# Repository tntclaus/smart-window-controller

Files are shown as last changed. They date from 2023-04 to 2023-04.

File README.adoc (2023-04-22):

# Контроллер умного окна

[.float-group]
--
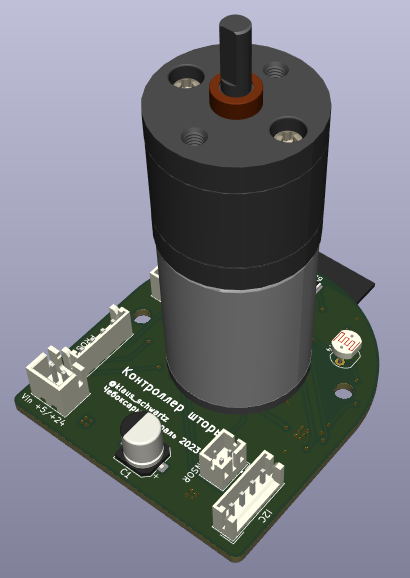
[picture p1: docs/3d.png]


Устройство для управления рулонной шторой. Умеет:

1. Прятаться внутри трубы рулонной шторы. Ставится с другого конца от механической крутилки и имеет такой же габарит. Механическая крутилка сохраняется т.к. вручную шторами тоже удобно управлять.
2. Двигать шторой, в том числе зеброй.
3. Датчиком освещенности следить, чтобы шторы пропускали необходимое количество света.может делиться этой инфой с другими шторами.
4. Датчиком холла контролить текущее положение шторы, даже если шторой управляют вручную через цепочку.
5. Автокалибровать положения полностью свернутой шторы концевиком если пропало электричество и штору двигали вручную.
6. Общаться с дополнительной переферией по i2c / uart (если есть).
7. Опрашивать датчик открытого окна (если есть).
--

## Печатные платы

Дизайн в kicad. Печатная плата распаивается непосредственно на двигатель.

[.float-group]
--
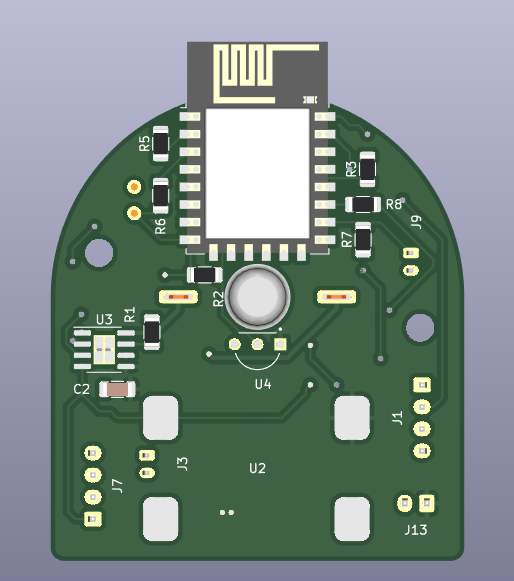
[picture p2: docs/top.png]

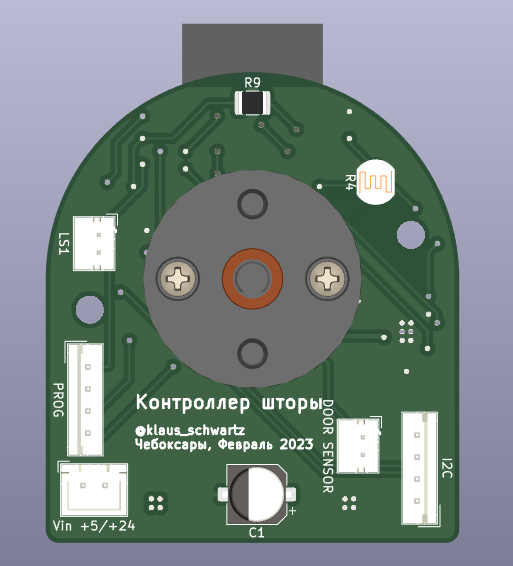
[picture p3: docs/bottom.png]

--

## Корпус и другие детали

Печатается на 3D принтере. Дизайн в openscad. Часть деталей предназначена для стыковки вала двигателя с трубой
для рулонных штор ø32мм, остальная часть — для крепления двигателя и печатной платы к окну/стене/раме.

Список деталей:

. Чехол для стыковки вала и трубы 32мм;
. Корпус контроллера с хомутным соединением с корпусом двигателя и винтовым с печатной платой;
. Кронштейн для крепления к окну конца трубы с двигателем;
. Звездочка для шариковой цепи с креплением к 32мм трубе;
. Кронштейн для крепления к окну конца трубы со звездочкой.

## Покупные компоненты

. Ткань для рулонной шторы;
. Труба для рулонных штор ø32мм;
. Двигатель с редуктором JGA25-370;
. Блок питания AC 220 -> 12V для питания двигателя;
. Полномостовой драйвер A4950;
. DC-DC преобразователь 5-25V -> 3.3V;
. ESP8266-12E / ESP8266-12F;
. (опция) SMD или DIP фоторезистор (LDR) — для них на плате предусмотрено 2 места. Можно сделать выносным.
. (опция) концевой выключатель — подключается через JST-PH (2мм шаг) разъём. Open drain.
. (опция) датчик открытия окна — подключается через JST-PH (2мм шаг) разъём. Open drain.
. (опция) I2C периферия — подключается через JST-EH (2.5мм шаг) разъём. Питание 3.3В.
. (опция) UART периферия — подключается через JST-EH (2.5мм шаг) разъём программирования. Питание нужно брать от разъёма I2C.

## Выбор двигателя

На 100-200 оборотов в минуту. Большее число оборотов теоретически может не дать нужного крутящего момента, меньшее число оборотов может сделать ручное раскручивание шторы проблематичным. Крутящий момент при 100 оборотах в минуту у большинства двигателей будет порядка 1 кг для барабана шторы с радиусом 2 см.

## Прошивка

Открытая прошивка ESPHome. Плата имеет разъёмы для загрузки собственной прошивки.

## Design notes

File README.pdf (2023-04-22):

# Контроллер умного окна

Устройство | для | управления
рулонной шторой. Умеет:

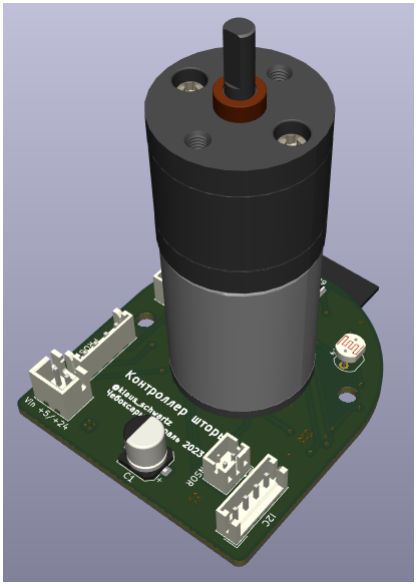
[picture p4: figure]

1. Прятаться внутри трубы рулонной шторы. Ставится с другого конца от механической крутилки и имеет такой же габарит. Механическая крутилка сохраняется т.к. вручную шторами тоже удобно управлять.
2. Двигать шторой, в том числе зеброй.
3. Датчиком освещенности следить, чтобы шторы пропускали необходимое количество света.может делиться этой инфой с другими шторами.
4. Датчиком холла контролить текущее положение шторы, даже если шторой управляют вручную через цепочку.
5. Автокалибровать положения полностью свернутой шторы концевиком если пропало электричество и штору двигали вручную.
6. Общаться с дополнительной переферией по i2c / uart (если есть).
7. Опрашивать датчик открытого окна (если есть).

# Печатные платы

Дизайн в kicad. Печатная плата распаивается непосредственно на двигатель.


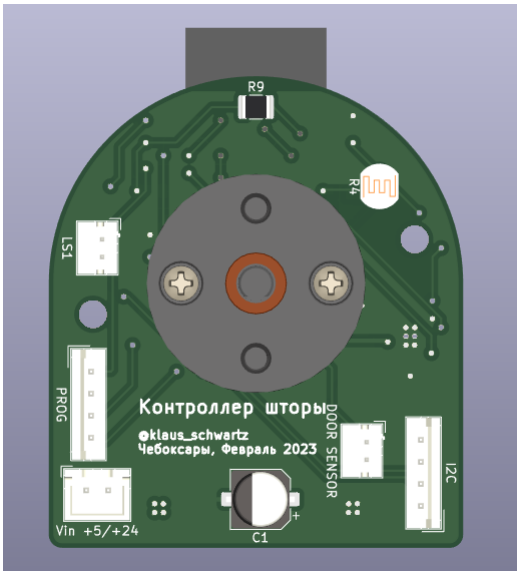
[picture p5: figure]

# Корпус и другие детали

Печатается на 3D принтере. Дизайн в openscad. Часть деталей предназначена для стыковки вала двигателя с трубой для рулонных штор ø32мм, остальная часть — для крепления двигателя и печатной платы к окну/стене/раме.

Список деталей:

1. Чехол для стыковки вала и трубы 32мм;
2. Корпус контроллера с хомутным соединением с корпусом двигателя и винтовым с печатной платой;
3. Кронштейн для крепления к окну конца трубы с двигателем;
4. Звездочка для шариковой цепи с креплением к 32мм трубе;
5. Кронштейн для крепления к окну конца трубы со звездочкой.

# Покупные компоненты

1. Ткань для рулонной шторы;
2. Труба для рулонных штор ø32мм;
3. Двигатель с редуктором JGA25-370;
4. Блок питания AC 220 → 12V для питания двигателя;
5. Полномостовой драйвер A4950;
6. DC-DC преобразователь 5-25V → 3.3V;
7. ESP8266-12E / ESP8266-12F;
8. (опция) SMD или DIP фоторезистор (LDR) — для них на плате предусмотрено 2 места. Можно сделать выносным.
9. (опция) концевой выключатель — подключается через JST-PH (2мм шаг) разъём. Open drain.
10. (опция) датчик открытия окна — подключается через JST-PH (2мм шаг) разъём. Open drain.
11. (опция) I2C периферия — подключается через JST-EH (2.5мм шаг) разъём. Питание 3.3В.
12. (опция) UART периферия — подключается через JST-EH (2.5мм шаг) разъём программирования. Питание нужно брать от разъёма I2C.

# Выбор двигателя

На 100-200 оборотов в минуту. Большее число оборотов теоретически может не дать нужного крутящего момента, меньшее число оборотов может сделать ручное раскручивание шторы проблематичным. Крутящий момент при 100 оборотах в минуту у большинства двигателей будет порядка 1 кг для барабана шторы с радиусом 2 см.

# Прошивка

Открытая прошивка ESPHome. Плата имеет разъёмы для загрузки собственной прошивки.

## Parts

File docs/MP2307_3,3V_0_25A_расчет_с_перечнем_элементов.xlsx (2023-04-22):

 | 3,3V 0,25A
https://www.monolithicpower.com/en/design-tools/design-tools/dc-dc-designer-online.html?PN=MP2307/
L1 | VLS6045EX-100M, 10 мкГн, 20%, Индуктивность SMD | чип-дип | 53 | рубля |  | https://www.chipdip.ru/product/vls6045ex-100m-10
или | Индуктивность 10 мкГн 700 мА LQH32PN100MN0L, Murata | в наличии
С1, С3, С4 | Конденсатор керамический 0805 10 мкФ 6.3 В 10 % X7R CL21B106KQQNNN, SAMSUNG | в наличии
С2, С9 | Конденсатор ЧИП керамический 0603 0.1 мкФ 50 В 10 % X7R CC0603KRX7R9BB104, Yageo | в наличии
С5, С7 | Конденсатор керамический 0603 0.01 мкФ 100 В 10 % X7R CL10B103KC8NNNC, SAMSUNG | в наличии
C8 | не устанавливаем
R1 | 26,6 кОм из 2х последовательных резисторов 0603 | чип-дип | Набор ЧИП резисторов 1 кОм-9.1 кОм |  |  | https://www.chipdip.ru/product0/9000545429
 |  |  | Набор ЧИП резисторов 10 кОм-91 кОм |  |  | https://www.chipdip.ru/product0/9000545430
R2 | 10 кОм из набора | чип-дип |  |  |  | https://www.chipdip.ru/product/0.1w-0603-6.2-kom-1
R5 | 0.1Вт 0603 6.2 кОм, 1%, Чип резистор (SMD) | чип-дип | 5 | рубля | или из набора | https://www.chipdip.ru/product/0.1w-0603-6.2-kom-1
R6 | 91 кОм из набора, или 100 кОм 0603 | чип-дип
R7 | не устанавливаем, влияет только на напряжение включения преобразователя

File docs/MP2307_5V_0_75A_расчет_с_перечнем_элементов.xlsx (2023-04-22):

 | 5V 0,75A
L1 | VLS6045EX-100M, 10 мкГн, 20%, Индуктивность SMD | чип-дип | 53 | рубля |  | https://www.chipdip.ru/product/vls6045ex-100m-10
С1 | Конденсатор ЧИП керамический 1206 10 мкФ 35 В 10 % X7R CL31B106KLHNNNE, SAMSUNG | в наличии
или | CC0805KKX7R7BB106, Чип конденсатор 0805 X7R 10мкФ 16В 10% | чип-дип | 12 | рублей | если место ограничено | https://www.chipdip.ru/product0/8012766320
С2, С9 | Конденсатор ЧИП керамический 0603 0.1 мкФ 50 В 10 % X7R CC0603KRX7R9BB104, Yageo | в наличии
С3, С4 | Конденсатор керамический 0805 10 мкФ 6.3 В 10 % X7R CL21B106KQQNNN, SAMSUNG | в наличии | 2 штуки параллельно
С5, С7 | Конденсатор керамический 0603 0.01 мкФ 100 В 10 % X7R CL10B103KC8NNNC, SAMSUNG | в наличии
R1 | 27,4 кОм из 2х последовательных резисторов 0603 | чип-дип | Набор ЧИП резисторов 1 кОм-9.1 кОм |  |  | https://www.chipdip.ru/product0/9000545429
 |  |  | Набор ЧИП резисторов 10 кОм-91 кОм |  |  | https://www.chipdip.ru/product0/9000545430
R2, R5 | 0.1Вт 0603 6.2 кОм, 1%, Чип резистор (SMD) | чип-дип | 5 | рубля | или из набора | https://www.chipdip.ru/product/0.1w-0603-6.2-kom-1
R6 | 91 кОм из набора, или 100 кОм 0603 | чип-дип
R7 | не устанавливаем, влияет только на напряжение включения преобразователя

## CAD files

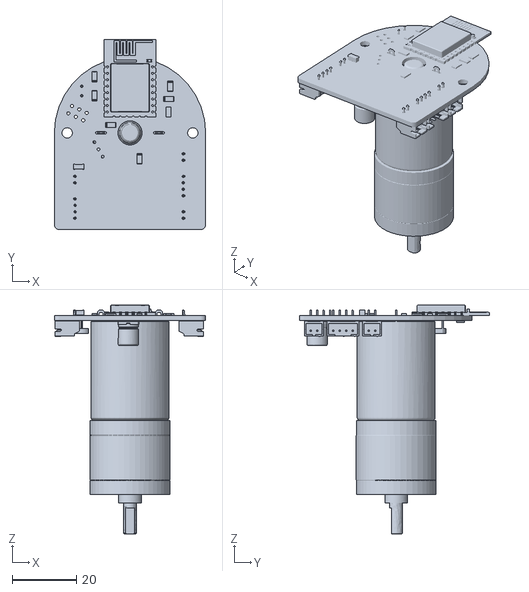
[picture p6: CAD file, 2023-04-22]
kicad/smart_curtain_controller.stl
47.0 x 59.0 x 71.1

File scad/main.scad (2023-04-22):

include <NopSCADlib/utils/core/core.scad>
//include <NopSCADlib/utils/core/core.scad>
include <lib/bead_chain_sprocket/bead_chain_sprockets.scad>


module motor_and_pcb() {
    translate([0,3.25,-5])
    color("silver")
    rotate([180,0,0])
    import("../kicad/smart_curtain_controller.stl");
}

TUBE_CONNECTOR_L = 50;
MOTOR_DIA = 25;
TUBE_DIA_OUTER = 38;
TUBE_DIA_INNER = TUBE_DIA_OUTER-1.2*2;

MATERIAL_DIA_OUTER = 56;

PCB_DIA = 48;

MOUNT_HOLES = [[18.5,3.5,0], [-18,-5,0]];
LDR_HOLES = [[-14,-11,0], [0,-18,0]];

module place_mount_holes() {
    for(hole = MOUNT_HOLES)
    translate(hole)
    children();
}

module place_ldr_holes() {
    for(hole = LDR_HOLES)
    translate(hole)
    children();
}

module material_tube(l = 400) {
    color("brown")
    difference() {
        cylinder(d = MATERIAL_DIA_OUTER, h = l-1);
        translate_z(-.1)
        cylinder(d = TUBE_DIA_OUTER+.2, h = l+2);
    }
}

module roller_tube(l = 400) {
    color("silver")
    difference() {
        cylinder(d = TUBE_DIA_OUTER, h = l);
        translate_z(-.1)
        cylinder(d = TUBE_DIA_INNER, h = l+.2);
    }
}

module controller_case_shape_sketch(s) {
    hull() {
        circle(d = s);
        translate([0,30,0])
        square([s,1], center = true);
    }
}

module controller_case_cover_stl() {
    stl("controller_case_cover");
    difference() {
        translate_z(.1)
        union() {
            cylinder(d = MOTOR_DIA + 3, h = 12);
            color("green")
            linear_extrude(1.5)
                controller_case_shape_sketch(PCB_DIA+3);
        }
        cylinder(d = MOTOR_DIA, h = 20);
        place_mount_holes()
            cylinder(d = 3, h = 20);
        place_ldr_holes()
            cylinder(d = 6, h = 20);
    }
}

module controller_case_base_stl() {
    stl("controller_case_base");
    difference() {
        translate_z(.1)
        union() {
            linear_extrude(1.5)
                controller_case_shape_sketch(PCB_DIA+3);
        }
        place_mount_holes()
        cylinder(d = 3, h = 20);
    }
}

module motor_tube_connector_stl() {
    stl("motor_tube_connector");

    color("white") {
        difference() {
            cylinder(d = TUBE_DIA_OUTER, h = TUBE_CONNECTOR_L - 1);
            translate_z(- .1)
            cylinder(d = TUBE_DIA_INNER, h = TUBE_CONNECTOR_L);
        }
        translate_z(TUBE_CONNECTOR_L - 1)
        difference() {
            hull() {
                cylinder(d = TUBE_DIA_OUTER, h = .1);
                translate_z(2)
                cylinder(d = TUBE_DIA_INNER, h = .1);
            }

            translate_z(- .1)
            hull() {
                cylinder(d = TUBE_DIA_INNER, h = .2);
                translate_z(2)
                cylinder(d = TUBE_DIA_INNER - 1.2 * 2, h = .25);
            }
        }

        translate_z(TUBE_CONNECTOR_L)
        difference() {
            cylinder(d = TUBE_DIA_INNER, h = 10);
            translate_z(- .1)
            difference() {
                cylinder(d = 4.3, h = 12);
                translate([- 2, 1.65, 0])
                    cube([4, 4, 12]);
            }
        }
    }
}

module controller_case() {
    controller_case_cover_stl();
    translate_z(-10)
    controller_case_base_stl();
}

module bead_chain_sprocket_top_stl() {
    bead_chain_sprocket_half(BEAD_CHAIN_4x2x28);
}

module bead_chain_sprocket_bottom_stl() {
    vflip()
    bead_chain_sprocket_half(BEAD_CHAIN_4x2x28);
}

module roller_curtain_assembly() {

    translate_z(-3.5){
        motor_and_pcb();
        controller_case();
    }
//    motor_tube_connector_stl();
    {
//        translate_z(TUBE_CONNECTOR_L)
//        roller_tube(l = 400-TUBE_CONNECTOR_L);
//        material_tube(l = 400);
    }
    translate_z(410){
        bead_chain_sprocket_top_stl();
        bead_chain_sprocket_bottom_stl();
    }
}

rotate([0,90,0])
roller_curtain_assembly();

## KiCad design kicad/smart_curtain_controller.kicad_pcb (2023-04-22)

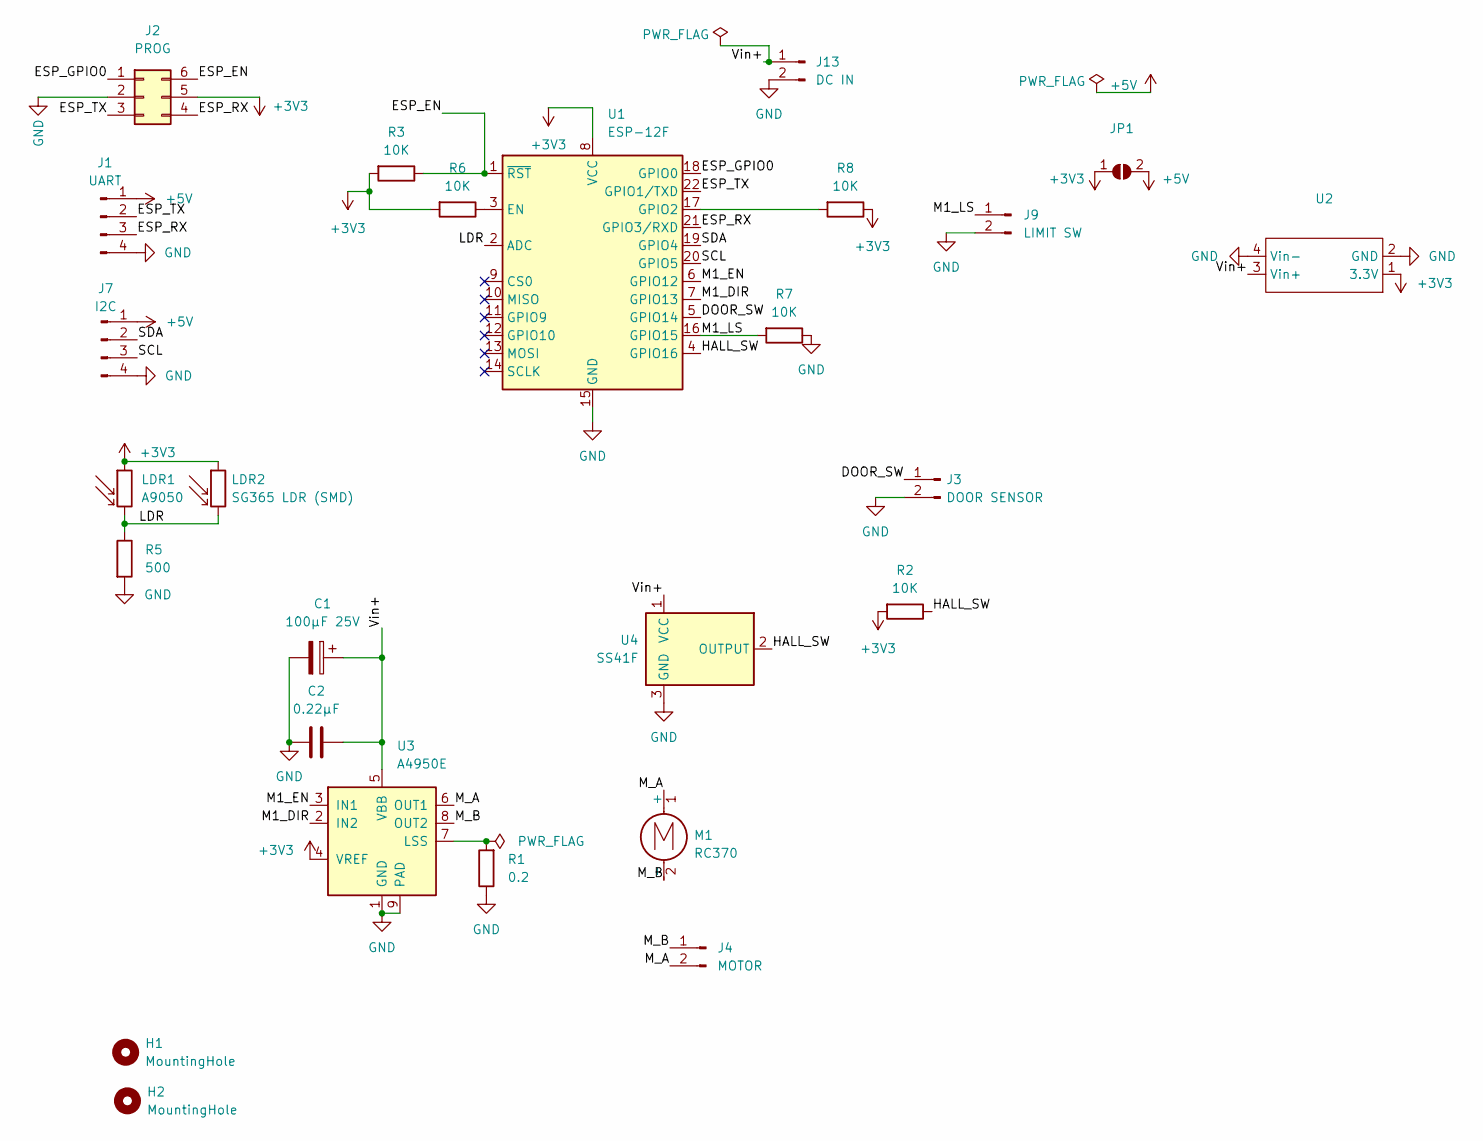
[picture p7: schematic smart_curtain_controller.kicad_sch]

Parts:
C1: 100µF 25V; CP_Radial_D6.3mm_P2.50mm
C2: 0.22µF; C_1206_3216Metric
H1, H2: MountingHole; MountingHole_3.2mm_M3
J1: UART; JST_PH_S4B-PH-K_1x04_P2.00mm_Horizontal
J2: PROG; PinHeader_2x03_P2.54mm_Vertical
J3: DOOR SENSOR; JST_PH_S2B-PH-K_1x02_P2.00mm_Horizontal
J4: MOTOR; JST_PH_S2B-PH-K_1x02_P2.00mm_Horizontal
J7: I2C; JST_PH_S4B-PH-K_1x04_P2.00mm_Horizontal
J9: LIMIT SW; JST_PH_S2B-PH-K_1x02_P2.00mm_Horizontal
J13: DC IN; JST_PH_S2B-PH-K_1x02_P2.00mm_Horizontal
JP1: (no value)
LDR1: A9050; R_LDR_5.0x4.1mm_P3mm_Vertical
LDR2: SG365 LDR (SMD); R_1210_3225Metric
M1: RC370
R1: 0.2; R_1206_3216Metric
R2, R3, R6, R7, R8: 10K; R_1206_3216Metric
R5: 500; R_1206_3216Metric
U1: ESP-12F; ESP-12E
U2: (no value)
U3: A4950E; SOIC-8-1EP_3.9x4.9mm_P1.27mm_EP2.41x3.3mm
U4: SS41F; Hall_Switch_TO-92

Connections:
+3V3: J2.5, JP1.1 (A), LDR1.1, LDR2.1, R2.2, R3.2, R6.2, R8.1, U1.8 (VCC), U2.1 (3.3V), U3.4 (VREF)
+5V: J1.1, J7.1, JP1.2 (B)
/DOOR_SW: J3.1, U1.5 (GPIO14)
/ESP_EN: J2.6, R3.1, U1.1 (~RST)
/ESP_GPIO0: J2.1, U1.18 (GPIO0)
/ESP_RX: J1.3, J2.4, U1.21 (GPIO3/RXD)
/ESP_TX: J1.2, J2.3, U1.22 (GPIO1/TXD)
/HALL_SW: R2.1, U1.4 (GPIO16), U4.2 (OUTPUT)
/LDR: LDR1.2, LDR2.2, R5.1, U1.2 (ADC)
/M1_DIR: U1.7 (GPIO13), U3.2 (IN2)
/M1_EN: U1.6 (GPIO12), U3.3 (IN1)
/M1_LS: J9.1, R7.2, U1.16 (GPIO15)
/M_A: J4.2, M1.1 (+), U3.6 (OUT1)
/M_B: J4.1, M1.2 (-), U3.8 (OUT2)
/SCL: J7.3, U1.20 (GPIO5)
/SDA: J7.2, U1.19 (GPIO4)
/Vin+: C1.1, C2.2, J13.1, U2.3 (Vin+), U3.5 (VBB), U4.1 (VCC)
GND: C1.2, C2.1, J1.4, J2.2, J3.2, J7.4, J9.2, J13.2, R1.1, R5.2, R7.1, U1.15 (GND), U2.2 (GND), U2.4 (Vin-), U3.1 (GND), U3.9 (PAD), U4.3 (GND)
unnamed: R1.2, U3.7 (LSS)
unnamed: R6.1, U1.3 (EN)
unnamed: R8.2, U1.17 (GPIO2)

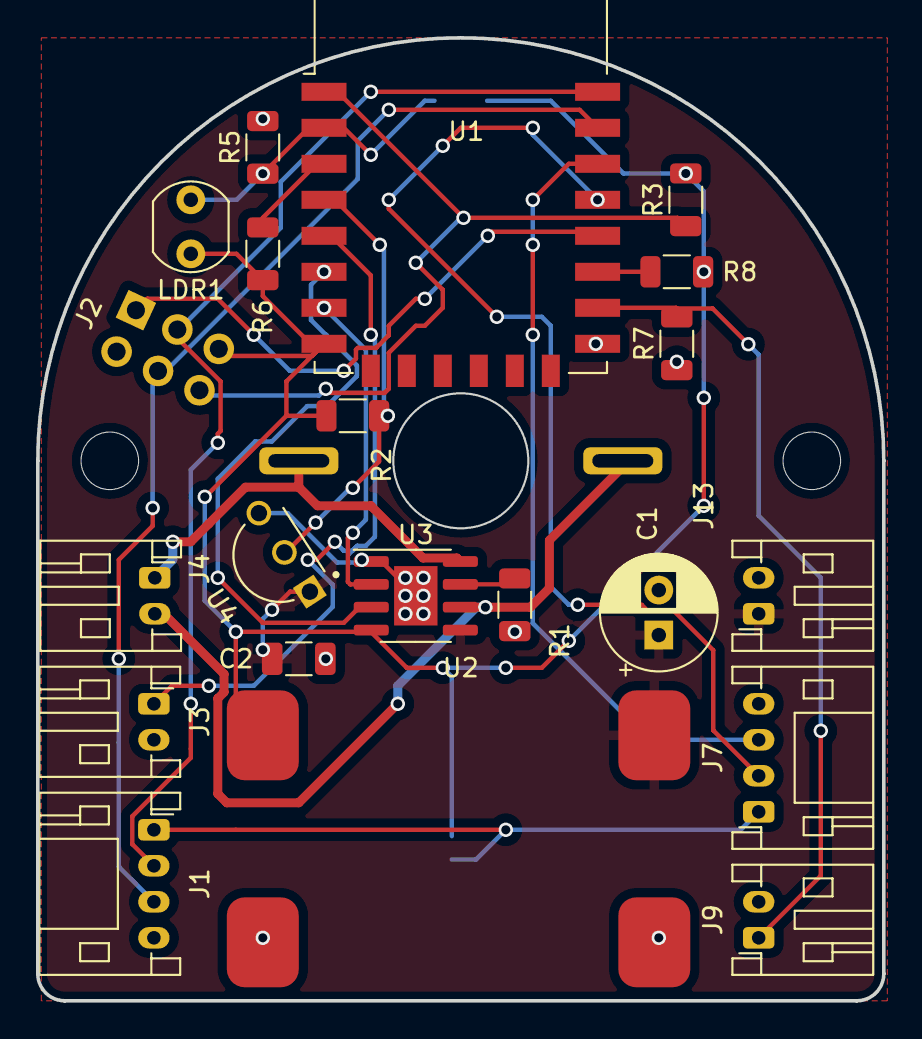
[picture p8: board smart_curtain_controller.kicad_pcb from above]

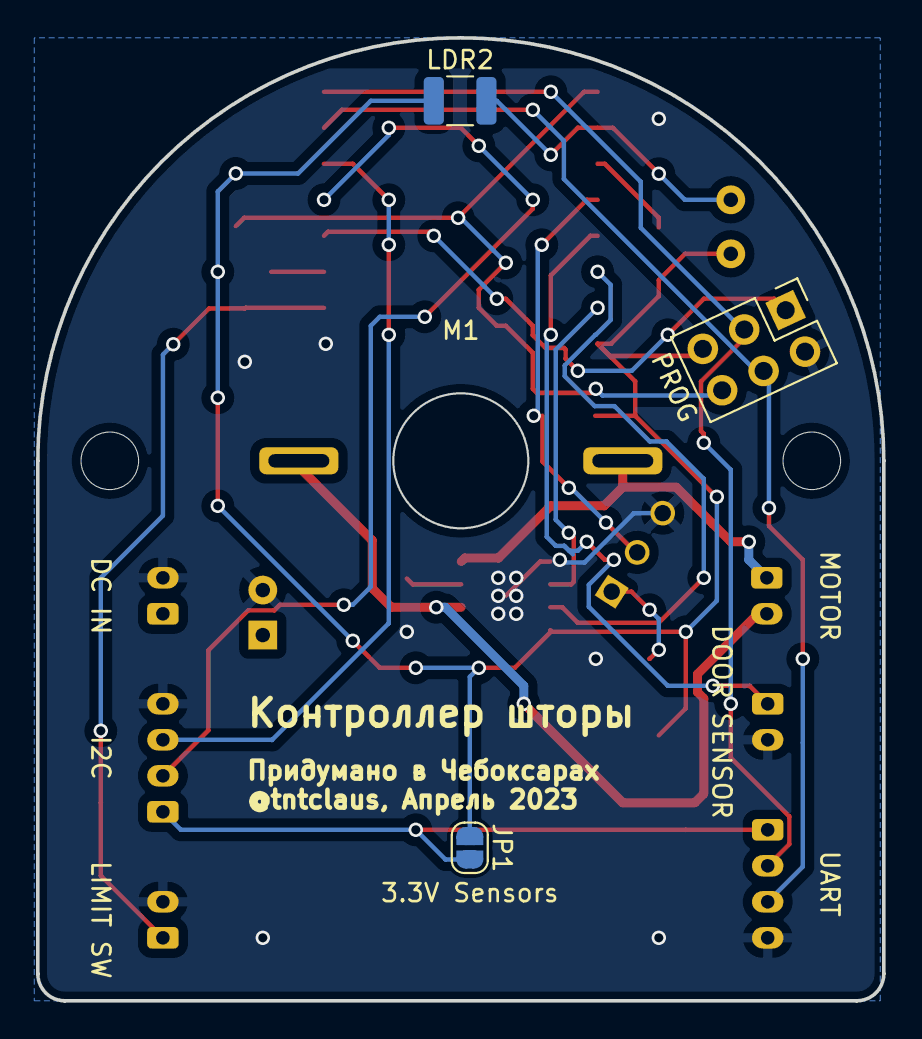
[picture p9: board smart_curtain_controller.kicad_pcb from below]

Board: 2 copper layers, 47.0 x 53.5 mm, 26 parts (4 on the bottom side), 21 nets.

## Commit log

2023-01-01 Первая версия
    [h_bridge.kicad_sch, smart_window.kicad_pcb, smart_window.kicad_sch]
2023-01-01 добавил фотосенсор
    [smart_window.kicad_pcb, smart_window.kicad_sch]
2023-01-01 добавлен DC-DC преобразователь для питания 3В от БП двигателя
    [smart_window.kicad_pcb, smart_window.kicad_sch]
2023-01-19 версия с мостами на биполярных транзисторах
    [smart_window.kicad_pcb]
2023-01-20 вариант с микросхемами a4950
    [h_bridge.kicad_sch, smart_window.kicad_pcb, smart_window.kicad_sch]
2023-01-20 изменено положение монтажных отверстий
    [smart_window.kicad_pcb]
2023-01-23 2-сторонняя версия
    [smart_window.kicad_pcb, smart_window.kicad_sch]
2023-04-22 simple version that should work
    [12v25v.kicad_sch, MP2307_3,3V_0_25A_расчет_с_перечнем_элементов.xlsx, MP2307_5V_0_75A_расчет_с_перечнем_элементов.xlsx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]
